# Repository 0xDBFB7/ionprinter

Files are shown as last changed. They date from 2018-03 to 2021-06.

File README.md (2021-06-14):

```
    _                       __        _  __   __  
   (_)____   ____   ____   / /____   (_)/ /_ / /_ 
  / // __ \ / __ \ / __ \ / // __ \ / // __// __ \
 / // /_/ // / / // /_/ // // /_/ // // /_ / / / /
/_/ \____//_/ /_/ \____//_/ \____//_/ \__//_/ /_/ 
```                                        

# Ionolith

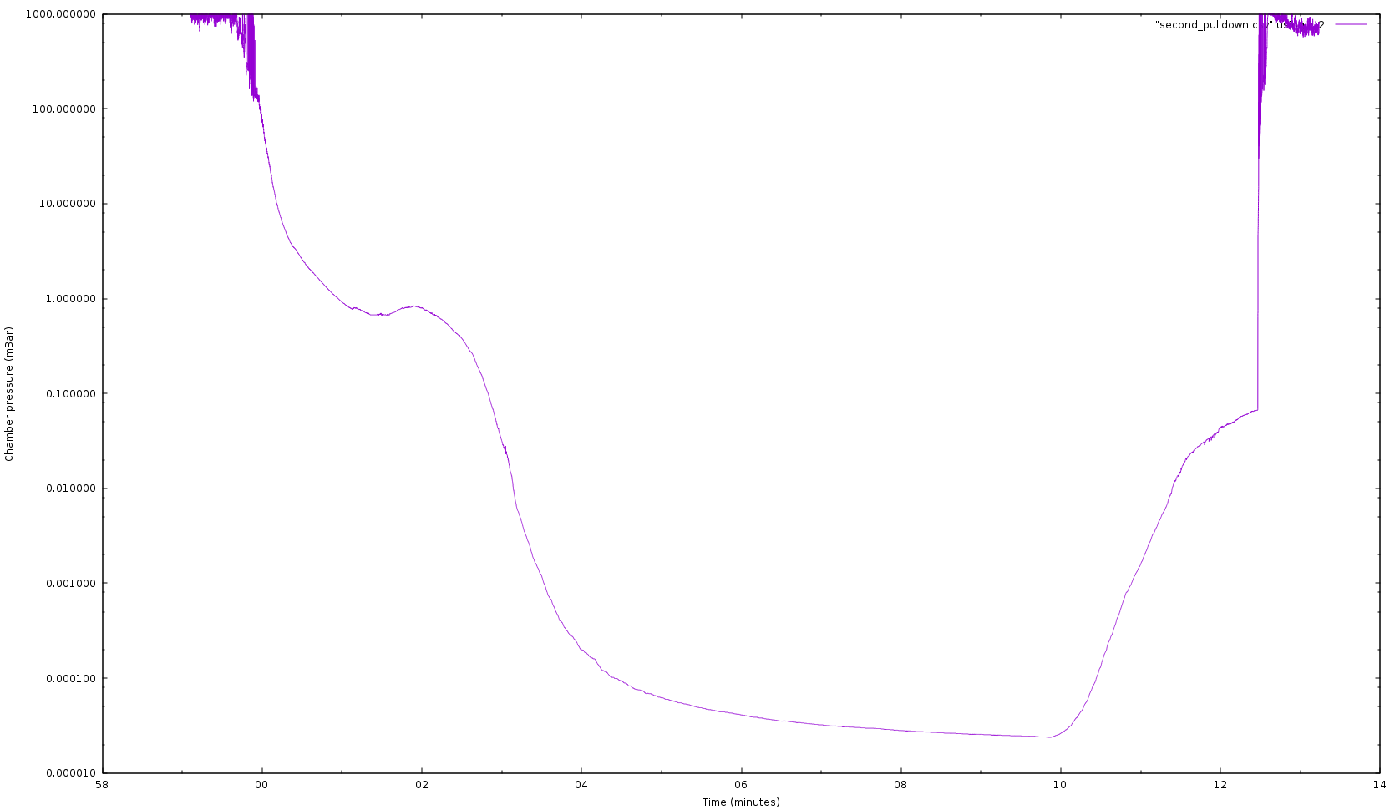
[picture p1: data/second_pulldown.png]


Hardware, firmware, software, and documentation for ion printers.

This was an extremely speculative (and arguably pseudoscientific) project to attempt to scale up physical vapor deposition beyond all reasonable limits. I got as far as building a high vacuum chamber, testing a few "bowtie" crucible designs, etc.

Spinoffs:

- a GPU-accelerated Particle-In-Cell program called [Nyion](https://github.com/0xDBFB7/Nyion) 
- A cheap silicon carbide [furnace](https://0xdbfb7.com/furnace.html)
- A cheap controller for Varian Turbo-V200 series of pumps [varian-turbo-controller](https://github.com/0xDBFB7/varian-turbo-controller)
- Control software for an Inficon BPG-400 vacuum gauge [gauge.py](https://gist.github.com/0xDBFB7/7bd7048c6639270e6f291a2673903184)

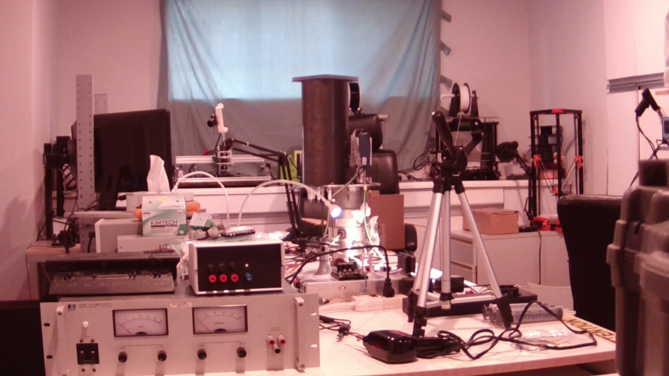
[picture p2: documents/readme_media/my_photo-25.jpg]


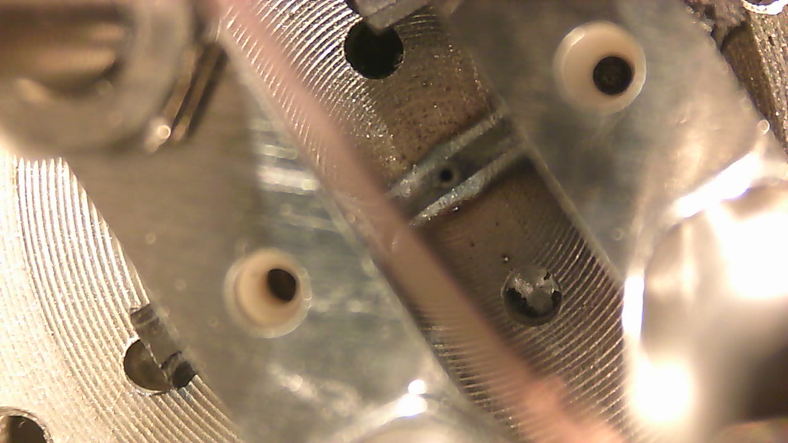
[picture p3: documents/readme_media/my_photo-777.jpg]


This whole project was far beyond my capabilities, suffers from a lack of basic physical modelling in the beam region, and so there is little basis to expect this to work.

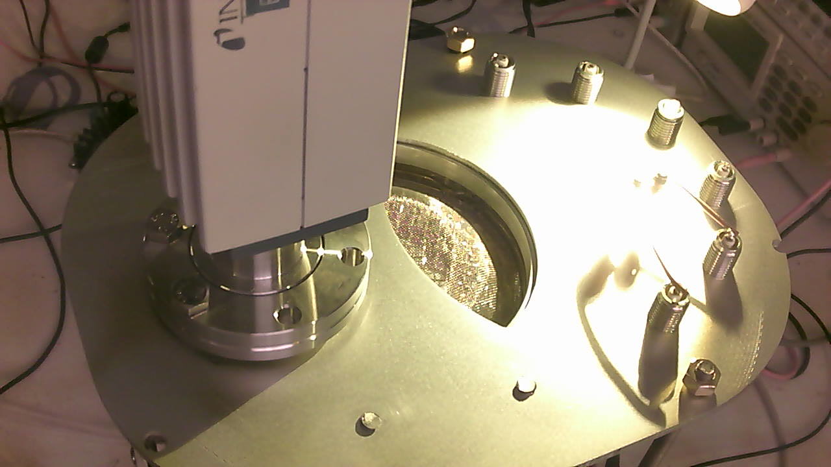
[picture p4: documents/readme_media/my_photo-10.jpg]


At the time the project was suspended, it looked something like this:

The ultimate goal was to produce an ultra high current (somewhere around 100 A of ionized aluminum accelerated to 100 to 1000 eV) heavy ion beam deposition system, aiming to 3D print large parts at cubic centimeters per hour and with arbitrary combinations of alloys and crystalline structure. 

  - Heavy ions like Al move slowly, meaning space charge effects are huge and, due to so-called "beam rigidity", magnetic focusing is useless.
  - However, this was developed under the (as yet untested assumption) that it would be possible to use a sort of active space-charge neutralization, actively injecting and confining electrons into metal-ion "packets" in the beam, to neutralize the beam space charge (something like [Gotoh 2012]).
  - Spreading the beam current over 512 or 1024 individually-controlled emitters in a 0.25 m^2 area seemed like it might alleviate deposition surface roughness issues, because of the wide range of angles of incidence.(See [Yang and Zhou, 1999, 2001])
  - Feedstock would be vaporized in "bowtie" structure - perhaps graphite-loaded magnesium oxide, perhaps coated in aluminum nitride, and with layers of ceramic multi-layer insulation to mitigate heat loss. Basic testing on a graphite bowtie was done.
  - Design goal of <$2000 cost, ideally run from a single 1500w outlet, with integrated diffusion pump.
  - Acceleration voltages over ~5000 V would pose huge X-ray and general power consumption (dozens of kilowatts in the beam!) and deposition power density (build platform overheating) issues.

```
Gotoh Y, Tsuji H, Taguchi S, Ikeda K, Kitagawa T, Ishikawa J, et al. Neutralization of space charge on high-current low-energy ion beam by low-energy electrons supplied from silicon based field emitter arrays. AIP Conference Proceedings, vol. 1496, 2012, p. 368–71.
Zhou XW, Wadley HNG. Hyperthermal vapor deposition of copper: reflection and resputtering effects. Surface Science 1999;431:58–73. https://doi.org/10.1016/S0039-6028(99)00336-2.
Yang YG, Zhou XW, Johnson RA, Wadley HNG. Monte Carlo simulation of hyperthermal physical vapor deposition. Acta Materialia 2001;49:3321–32. https://doi.org/10.1016/S1359-6454(01)00139-2.
```

For all references involved, see the file references.bib.

# <3     

# :D

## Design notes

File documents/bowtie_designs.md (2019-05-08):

```BowtieML
x = 4-40 threaded rod
(o) = alumina ionization column
o = RF coil
I = z pinch magnet
= or - or _ or O = graphite
! = copper electrode

|x|=========( )=========|x| - top graphite heater to keep ionization column warm \
    II    o (o) o    II |x|				also acts as acceleration anode?
    II    o (o) o    II |x|
    II    o (o) o    II |x|
    II    o (o) o    II |x|
      x   o (o) o   x   |x|
    ||x|| o (o) o ||x|| |x|	- nested insulators and nuts
  !!!|x|! o (o) o !|x|! |x| - copper bowtie connectors
     |x|===-_O_-===|x| 	|x|	- bowtie and injector and threaded insulators
    ||x||		  ||x|| |x|	- nested ceramic insulators 
    -----------------------	- aluminium base with blind 4-40 tapped holes
    
    Injector could be placed on the top. The top and bottom graphite heaters can be perpendicular.
    
Advantages:

Problems:
Collision with alumina wall is likely to cause high losses at high pressures.
No charge discrimination.

```

```BowtieML
Hybrid Pierce-type extractor/ICP

= - graphite
\/ - conductive but sufficiently RF transparent material - graphite?
|- - alumina insulator

			   - unspecified recombination wizardry
=====    =====
o|/        \|o - multi-segment deflection/astigmatism plates (optional)
o||		   ||o - alumina insulator ring - probably required at HV
o|\        /|o
o| \      / |o
o|  \	 /  |o - 50+kv electrostatic cone
-----    ----- - 
			   - standard graphite injection nozzle
			   
Electrostatic cone profile can be precisely adjusted to cancel out beam dispersion à la microwave dishes.

The beam must be recombined before exiting the focus chamber. 

Z-pinch and helical B-fields can be added to increase ionization efficiency; these won't affect the ions but will direct electrons. Care must be taken to ensure that these fields don't interfere with recombination.

Cone must be carefully positioned to prevent axial acceleration and the resultant X-rays. 

A phosphor+pmt interlock could be added for safety.

Why would the particles be compelled to move in a specific direction? With AC B input, would the entire arrangement not be perfectly symmetrical? 
```

```BowtieML
Hybrid Goertzel-type extractor

= - graphite
\/ - conductive but sufficiently RF transparent material - graphite?
|- - alumina insulator

			   - unspecified recombination wizardry
=====    =====
o|/        \|o - multi-segment deflection/astigmatism plates (optional)
o||		   ||o - alumina insulator ring - probably required at HV
o|-        -|o
o|--      --|o
o|- 	   -|o - 50+kv electrostatic focus structure
-----    ----- - 
			   - standard graphite injection nozzle

A reference structure is on p148 of Goerzel
```
```

```

```
      ||
      ||
      \
        \  |  |
      \   \|  |
      ||\	  |
      ||  \---|

The region where wire is injected must be colder than the melting point of the wire, else gas will escape. A large radiator can be attached to the nozzle.

```

``` 
()  = BaO coating or hot cathode
_   = high-resistance gradient deflector
--  = ceramic insulator
O   = ICP coil
[] 	= iron and mu-metal/pyrolytic graphite core and shield to prevent icp-recomb. interference
| | = graphite bowtie nozzle

   ||(     )||
   ||(_   _)|| 	    - recombination another fixed distance away
O] ----- ----- [O   - very small ~250um gap to stay within Langmuir limits
O] ----- ----- [O   - precise C-L-defined gap for ionization, +100v or so
	   | |		    - bowtie nozzle extension
 ======_O_======
 
 Entire structure can be heated to prevent deposition
```

```
:  = graphite "drawing die" injector
#  = injected wire
- 
--------------------||
-----------\		||
########## :========||
-----------/
----------------------------
 ^   	   ^	    ^ - transition to ideal vapor temperature occurs here
 |         | - transition to melting temperature occurs around here.
 |				gas-tight seal must be formed.
 | -This side radiatively cooled by graphite fins to below melting point

This may allow us to accept different gauges of wire.
```

<hr>

There are some difficulties in using ICP for this application - namely,

- Ambiguity in output particle energy spectrum
- Time-varying components leading to excessively complex simulations. Full analysis requires both small-scale timesteps to model collisions, and large-scale timesteps to model "butterfly" ion trajectories.
- Uncontrolled magnetic field - shielding from recombination current will likely be required

The main reason why I considered it in the first place was to obviate the need for a heavy and dangerous high-power, high-voltage transformer. 

However, the precise ionization cross section at 

However, the electron impact cross section for most of the elements we would choose peaks at below 

Lotz, Wolfgang. "Electron-impact ionization cross-sections for atoms up to Z= 108." *Zeitschrift für Physik A Hadrons and nuclei* 232.2 (1970): 101-107, https://link.springer.com/content/pdf/10.1007/BF01393132.pdf

```

, simple transverse-electron impact might be a simpler route.

```

```
The ion and recombination beams must be precisely matched for recombination to occur - see relativistic argument. 

The e-beam can be bent into alignment by a small magnetic field:

| / - wasted recomb. electrons
|(  - recombination point
| \ - e-beam gun

This would allow precise control over the recombination position - essential for accurate deposition.

This also allows the recombination beam energy to be varied independently, as the B-field will not affect the heavy beam.

\ | /
 )|(
/ | \

An axial field may also aid in recombination.
```

```
Low-energy design 1

After many months were spent attempting to design a focusing lens capable of 

Each bowtie is ~1mm in radius and carries 0.04 milliamps of beam current. Somewhere around 250,000 bowties will be required.

|   |   |   |   - focus and 
--o---o---o--

The bowties are arranged in concentric rings. Each ring has a different focus voltage applied passively through a resistor divider, a'la PMT electrodes.

```

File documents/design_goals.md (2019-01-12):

### Print materials

Aluminum and Copper were my target metals. I originally planned on testing with Zinc, due to its low boiling point. However, pure zinc wire is quite difficult to come by, so I couldn't do testing with injector feed systems. 

The design isn't validated with any other materials, though anything that can survive ionization (single elements, essentially - compounds will be quite thoroughly destroyed) and has reasonable boiling temperatures and ionization energies should work.

### Cost

It would suck to build this only to have it be reserved for institutions or companies: it must be affordable to the hobbyist, like current 3d printers. 

Including high vacuum pump but excluding the external roughing pump (~$200) must cost less than $1000 to build.

### Print speed

I figured 40 grams per hour was a reasonable starting point - 2.232×10^20 atoms of aluminium per second. For comparison, current FDM 3d printers can usually do somewhere around 10g/h. Since aluminum has around 3x the density of PLA, however, the volumetric print speed will be nearly on par.

Aluminum is much stronger than PLA, though, so thinner walls and lower density infills can be used.

### Power consumption

For reasons described later, power is a significant constraint. The unit should be compatible with a standard 15-amp breaker, so the maximum power consumption has to be less than 1800 watts - 1400 watts or so after power supply losses.

### Shipping

International shipping'll be insane if this thing weighs more than 15-20kg. Some sort of telescopic arrangement would be ideal.

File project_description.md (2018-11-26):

Project:
===
Status:
-------

#### Date started: 2016-??-??
#### Date finished: 2017-??-??
#### Date written: 2017-08-14

Background:
---

Description:
---

---

Thread milled the two holes for the 3/4 NPT feedthroughs - used an end mill to taper, a ball mill to finish and a 60 degree HSS tool in a boring bar to thread mill. I milled the thread in 6 passes, at 34% of 600 mm/m - 12k rpm. Coolant definitely required.

Leak.

Did a huge amount of reading (mainly Goebels et al and nasa ion thruster datasheets) over florida vacation, and I believe an inductively coupled plasma might be the way to go now. Currently, I don't really know what the charge on each droplet of aluminum is - how many atoms the vapour is composed of, etc. With a powerful enough ICP coil, I'll get full ionization for every single atom, making the math for deflection easier. With a mass flow rate of about 0.01g/s (easily achivable with the current 300w filament system), the complete ionization energy is somewhere around 500 watts. I've found an efficiency figure of 40% from a few ICP systems, so basically I need a 1kw RF supply. I think I'm going to go with an "induction heater"-style resonant ZVS royer driver - since everything's fully shielded, I don't think I'm going to have to worry about the frequency that much; and using a resonant system means I can skip antenna matching, which was an issue for me in the past. Good for testing, anyhow.

Mass flow rate: $$2.232×10^20 atoms/s, 0.01g/s$$ - about 40 grams an hour
2.407678×10^-18 j/atom - 15 ev, roughly $$1/2((29 amu)((10000m/s)^2))$$... roughly 500 watts of beam power.

Regarding the ICP ionization, the thermal velocity of the gaseous aluminum will be around 1.7 km/s, meaning at 250khz the atoms'll move around 7 mm before being ionized - if the coil isn't long enough, the atoms'll be out of the magnetic field by the time they leave.

Found an awesome paper that describes the behavior of 500khz plasmas. It seems like LF plasmas actually have some desirable properties over the standard 13.56mhz ISM plasmas, once you get past E-mode - high uniformity, etc. LF is also much easier from a generator standpoint.

I think I'm going to transition to an "untapped" royer topology - this'll mean I only need two high current feedthroughs.

A 12mm diameter 25 mm long 5-turn air-core inductor has an inductance of roughly 0.00012755 millihenries. A resonant frequency of 500 khz will require a tank capacitance of around 0.8 microfarads. I want to err on the side of higher frequency, I think, so...

Whipped up a few LTspice simulations, found I needed inductance on the input (naturally), but it seems like I could actually just use a h-bridge on the high side...

Tested out the chamber a few more times, still leaking at the feedthroughs. Need to re-design them.

<lots of stuff happens off-camera>

Oh jeez.

This is going to have to be fast.

Really fast.

With a 100g/h deposition rate, a 10 mil dot size, and reasonable Z resolution of somewhere around 5 mil, the slew time of the deflection supplies will have to be under 50 us.

With a 10 mil dot size over a 1 cm deflection (400 steps), the slide will have to move at around $$1 cm/ 20 milliseconds$$ - around 40,000 mm/min. This seems just barely achievable with stepper slides.

With those same values and a requirement of 5 bytes per point, the software will have to stream points at nearly 100kbps. That seems achievable too. Proper curve fitting etc will also reduce that.

Values I'll probably have to update live:

- Beam X Y position, focus, astigmatism.
- Stepper X and Y position.
-

RF power, beam current, diffusion pump power, etc will presumably be set before a print.

I'm kind of coming to grips with how monumental the realtime requirements for this thing will be. I don't think I have any time to stream values to different processors - I think I'll have to abandon my original modular idea and make everything run on one STM32.

Now, the deflection amplifier.

Someone on phys.se raised a good point: at low acceleration voltages, how will stray magnetic fields affect the beam?

Since the magnetic force on a moving charge is F=qvB, the fuzzing due to magnetic fields should actually go down - but let's make sure.

At 48 eV, Aluminum will travel at 18,528 m/s. qvB at 100 gauss = -3×10^-17 newtons. The particles will take 2.7×10^-5 seconds to travel 0.5m to the build plate. This means that the beam will be slewed

0.5 * 6.695846×10^8 meters per second squared * (2.7×10^-5s)^2 = 0.2 meters.

Darn.

At 1 gauss, about 2.5 mm.

The deflection seems to be unrelated to V, but I know that this is impossible, since 30 kv CRTs aren't affected by the earth's magnetic field.

I must have something wrong in my reasoning. Going again:

(0.5*(((sqrt(2r)/sqrt(m))*b)/m)*(d/(sqrt(2r)/sqrt(m)))

Where r is energy, in eV.

R just falls out of the equation:

(0.5*b*d)/m

And so I am correct in that voltage is unrelated to magnetic deflection.

Wait, what?

Okay, looking it up, I'm totally wrong. The actual equation is:

X deflection = (0.5bd)*sqrt(q/(2(v)m))

Where v is volts. This means:

(0.5*(100 gauss* (0.5m)^2)) * sqrt(-(electron charge)/(2*48 volts *(27 amu in kg))) = 0.2 m.

At earth's magnetic field and 1000v, we get 0.1 mm. 100v: 0.5 mm. 48v: 0.7mm.

10 Gauss, 0.1m distance to build plate, and 48v: 1mm.

Now that, I believe, is fine - that's an N52 magnet at 0.1 m. Steady state components can be calibrated out, too - I'm mainly just worried about oscillating magnetic fields due to the RF coil.

With 150a going through the coil, there'll be a roughly 1.5 gauss field oscillating at 6 in away.

I can put a bunch of hall effect sensors in different places in the chamber and try to compensate for fields measured.

Aha! Existing induction heaters use inductors on the high side. When a piece of metal enters the coil, the frequency drops significantly - giving the inductor more time to allow more current through, increasing the power draw and dissipation. Cool!

Huh, wait. Why can't I just ionize the aluminum with bare +48v? The ionization energy of the aluminum is only like 15eV. If I can strike the arc with a few kilovolts (like a fluorescent tube), I should be able to ionize everything that goes through...

Hmm. Perhaps that "striking" effect relies on the gas already being ionized. That would make sense - but it'd also mean that I can't do that, since the gas is constantly being replenished.

Had an enlightening discussion on The H Bar about this striking effect; apparently it is related to the electron drift rate, and is likely to work on a stream of gas. Also, in 20170210_100824.mp4

When my milligram balance comes in, I'll try running a test with +48v and see what kind of ionization I can get - deposit onto a plate, measure the charge, weigh the plate, and divide by atomic mass of aluminum.

Going back to my graphite "bowtie" filament/crucibles; I can't find a reliable source on the resistivity of graphite, suprisingly enough; it seems to vary wildly between batches and processes. Measuring my block from McMaster, I get a value anywhere between 10 and 0.3 ohms with varying contact pressure. The block is 20.5 cm long by 2.5cm wide and 0.7cm thick. To get a slightly better reading, I connected up my Korad PSU to both ends and set it to 0.5a. This gave me a voltage of around 50-70mv and falling, for a resistance of around 1.5 ohms. Scaling that roughly to my previous bowtie's area, I get about 0.8 ohms. This explains why I didn't get good results with my previous bowtie tests at 20v; I'd only be drawing a few hundred watts. I'll have to try again with a smaller bowtie and with my new PSU.

Ooh, I could SPTM the graphite crucible! Nah, I don't need to.

Re: Speed: at 1Mbps, (about the peak for STM32 usb), transferring 1 point (6 floats; 4 bytes per float, no encoding) would take about 200 microseconds, plus response, which is longer than my target 50 us value. I guess I'll really have to fill up that buffer beforehand.

It seems like my ICP coil inductance value is incorrect: a more accurate value would be around 1 uh.
jb weld

Darnit. Another first-principles error; and I know why my many graphite/filament tests weren't working. With a surface area of 808 mm^2 (the v2 bowtie), and a temperature of 3070 K,
the bowtie will be radiating *nearly 4 kilowatts* as heat; the Stefan-Boltzmann law goes as the 4th power of temperature. The emissivity of tungsten is 0.04, which makes for a loss of 160w with the same area.

If I can get the bowtie surface area to below 20 mm^2, I'll only have to
contend with 100w of radiative losses, which seems manageable. Power budget is being eaten into a bit, but oh well.  I could also try using an aluminum reflector to increase efficiency;
aluminum is 87% reflective at infrared.

GAH; another bloody problem. If an alloy is injected into the bowtie, the different molecular masses will cause a "mass spectrometer" effect in the deflection plates, blurring the deposition horrendously.
Since we need to deposit all the materials in the alloy simultaneously, not sequentially, multiple bowties with multiple accleration voltages tuned to their respective masses would work.

Wire feedthroughs: Buna-N has a TML of around 7; I don't even have to worry about a tiny bit of JB-weld, I don't think.

The Bowtie; the graphite that I purchased from mcmaster has an exceptionally low resistivity; around 1.54×10^-5 ohm meters. This means that a 10mm long 4*4mm rod would have a resistance of 0.0385 ohms,
drawiing 20a at 12v. When the injector holes are drilled, and some extra contact resistance is added, this is almost perfect...though this bowtie would also have an area of 80mm^2; a loss of 400w.

Might have some issues dissipating 500-odd watts of beam power in a cm^3 scale part. Liquid-cooled or cryo-chilled build platform might be required.

Even at a super slow print speed of 0.4 g/h, a 1 oz PCB will be done in 17 hours.

A serious problem: the beam current density is much, much higher than standard particle accelerators. A typical value seems to be 50 A/m^2; with a beam diameter of 0.5 cm, the initial beam current density will
be nearly 125,000. A beam diameter of 1 cm will yield a current density of 31,800; but the electrostatic optics become problematic at these charge density levels.

So, I either have to decrease my beam power (how?), or figure out how to focus at that power.

I could split the beam into seperate beams, each with a lower energy...

A small dot size is only required for fine details, where the print speed can be lower.

Some simple math: 40g/h of aluminum, which is 15 cubic centimeters (a cube 2.46cm to the side).

Tested the micro stepper injector motor: good torque at raw 5v from an arduino even up to 240rpm. It has an unusual 8-10-9-11 pinout, strangely.

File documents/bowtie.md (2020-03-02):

# The ion printer first requires a thin, vaporized jet of the target material. 
## This page describes the element that creates this stream.

### Why the hell do you call it a "bowtie"?

The original prototype of this element bore a close resemblance to a bow-tie:



Bowties are cool, and I love me some whimsical industry-specific jargon (c.f. [salad-bowl](http://projects.astec.ac.uk/ERLPManual/index.php/Photo_Cathode_Heat_Cleaning), Schlooping). "Filament" is ambiguous - there are at least three other filaments in use. I'm sure there's some accepted industry-standard name for this kind of thing, so call it whatever you want.

### Wait, isn't this already a solved problem?

While thin-film PVD boats and baskets exist, they really aren't a good fit for this device for a few reasons.

* Firstly, and perhaps most importantly, they don't produce a thin stream of gas. They produce a cloud of atoms with essentially random direction. This might not seem like a huge deal, but it's what took the majority of the time developing the ion printer. You might think that a nozzle or aperture would work; but your nozzle has to also be heated to above ~3000 K, else all your gaseous aluminum sticks to the nozzle and rapidly prevents operation.
* Secondly, while even more specialized solutions may exist, they're bloody expensive. Even cheap tungsten boats seem to start at ~$100 - far too expensive for a consumer device.

### Required temperature

https://www.iap.tuwien.ac.at/www/surface/vapor_pressure

The vapor pressure of the desired print materials is low at low temperature.

Therefore, to get a bearable print speed of >50g/h, it can be assumed that boiling is required. 

### Why not use induction heating?

I spent a few thousand hours trying high-power induction heating methods (largely based on some papers I've since lost and [1]). Induction heating, however, has a few serious drawbacks compared with simple Joule heating:

* Low effectiveness on non-ferrous metals. Metals like iron love induction welding, due to their high relative permeability; Aluminum doesn't absorb current as well; sure, you can get a chunk of aluminum up to 800c or so with 10kw of power, but we don't have the luxury of such high powers.
* Low effectiveness above the Curie point. Metals generally lose a lot of their magnetic properties above a certain temperature; that temperature is far, far below their boiling point.

It may be possible to build an ion printer that uses induction heating, but there aren't many benefits.

### Why even use a filament? Why not just vaporize the material itself?

First of all, if you just apply a few kilowatts to some aluminum, it will simply melt apart, breaking the connection. This might seem simple to mitigate, but I couldn't find a way to do it. A sharp rising edge in the power domain is therefore required.

I did quite a bit of testing with large capacitors in an attempt to accomplish this, which was mildly successful. You can pretty easily dump a few KJ into some aluminum wire to get gaseous aluminum. Unfortunately, there's one serious issue with this: it's non-directional. Everything in the line-of-sight gets coated in aluminum, which is undesirable for long-term usage; it also becomes extremely difficult to form a beam with a spherical vapor cloud. It *may* be possible to electrostatically pull a cloud of neutral aluminum into a coherent beam, perhaps with an ICP coil surrounding the whole lot, but I gave up on this method.

### Some simple physics background:

To reach the boiling points of metals, extraordinarily high temperatures are required, and so heat loss minimization is paramount. Some ways that the bowtie will lose heat:

#### Convection

The bowtie is in a high vacuum, so thermal convection can be entirely neglected.

#### Radiation

Anything hotter than absolute zero radiates away thermal energy in the form of infrared radiation; the amount of energy loss is given by the [Stefan-Boltzmann Law](http://hyperphysics.phy-astr.gsu.edu/hbase/thermo/stefan.html).

This is proportional to emissivity and heated surface area, and goes as the 4th power of the temperature.



This power loss is quite significant. 

#### Enthalpy

Aluminium:

| Source | Energy requirement |
| --- | --- |
| Heating | 0.9 kJ/kg/K * 2500 degrees = 2250 kJ/kg |
| Fusion | 398 kJ/kg |
| Vaporization | 10.5 MJ / kg |
| Total | 13.15 MJ/kg |
| @40g/h | 144.7 W |

A print speed of 40g/h will require at least 144.7 watts to be input to the bowtie. Values for copper are similar.

### Tungsten filaments

#### Tungsten has a few things going for it:

* Insanely high melting point (3800K or so); essentially anything you could possibly want to vaporize could be done with a tungsten bowtie.
* Low emissivity (0.05 or so); this means that very little of your energy 
* It's already commonly used for thin-film thermal PVD systems
* It's inexpensive and readily available in the form of "Green" TIG electrodes.
* It's relatively inert, and won't react substantially with filament material

#### It's also got some pretty serious issues:

It's very difficult to work with. It's one of the hardest materials around, which makes conventional subtractive manufacturing processes nearly impossible; EDM/[ECM](https://nptel.ac.in/courses/112107077/module3/lecture15/lecture15.pdf) seems to be required. Standard casting techniques don't work; a complex high-pressure sintering process is required. There are many companies around that will wrangle this metal of Cthulhu to your desires, but that takes us far from the protective margins of vertical integration.

You might wonder why we even need to work the tungsten at all. Indeed, just winding some aluminum wire around a 1/16" tungsten rod produces a small bead of molten aluminum, which then evaporates. Unfortunately, this has the same problem as the capacitor discharge system above; it's not a directed stream of gas.

However, there is one process you can easily perform on tungsten: you can bend it. Though its melting point proper is high, it becomes very ductile at comparatively low temperatures; ~1500c - easily attainable with an acetylene torch. 

In retrospect, this seems obvious, but I learned it relatively late in the project.

A layer of yellow tungsten oxide forms when bending, which can be eliminated by using an inert (nitrogen, in my case) or endothermic atmosphere, but this layer quickly evaporates when the finished product is heated in a vacuum.

My final tungsten design was a cylinder wound using 1/16" tungsten rod, with a graphite plug at the bottom. This worked reasonably well. However, the efficiency and rate of vaporization was quite poor; with my high-current transformer, I was only just able to get to the boiling point of aluminum.

### Graphite

Graphite, on the other hand, is easily workable with standard machine tools. However, this comes at a cost:

* Poorly-defined properties. Graphite's electrical and thermal conductivity is dependent on a large number of factors, including grain size, production method, contact pressure, impurities, etc. It's even anisotropic; measuring resistance lengthwise or widthwise can return a different result. 
* More reactive. Graphite is prone to reacting with metals at high temperatures, though it remains to be seen how much of an issue this will be. The bowtie is likely to be an inexpensive consumable for this reason. 

Graphite also sublimates at high temperatures; its vapor pressure is between 10 and 100 Pa at the boiling point of aluminum.

There's kind of an issue here. Making the supports thicker decreases their resistance, allowing the crucial center section to become hotter; but it also increases their thermal conductivity proportionally, wicking heat away from the center section.

#### Ceramics

Thermal conductivity.

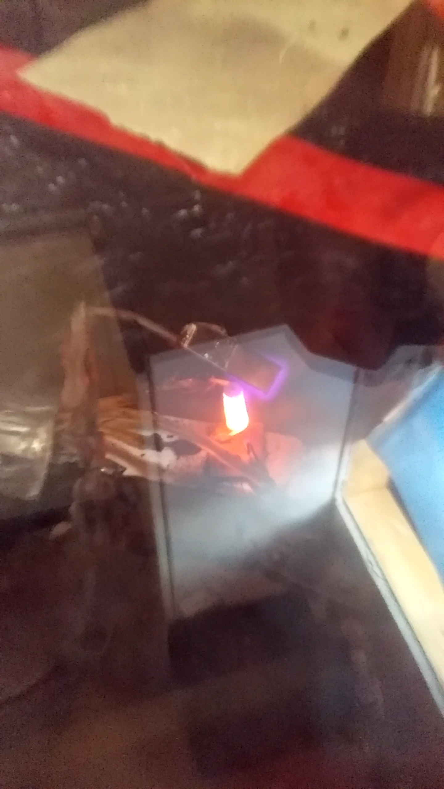
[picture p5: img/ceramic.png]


#### Zinc crucibles

For initial exploratory research, I attempted to vaporize zinc in my Gen1 and Gen2 test chambers, due to its ease of boiling. This worked okay, and helped me understand more about how how the vapor paths would work.

I attempted a number of zinc crucible designs, including using off-the-shelf heaters, sand resistors, etc, and finally settled on this one:

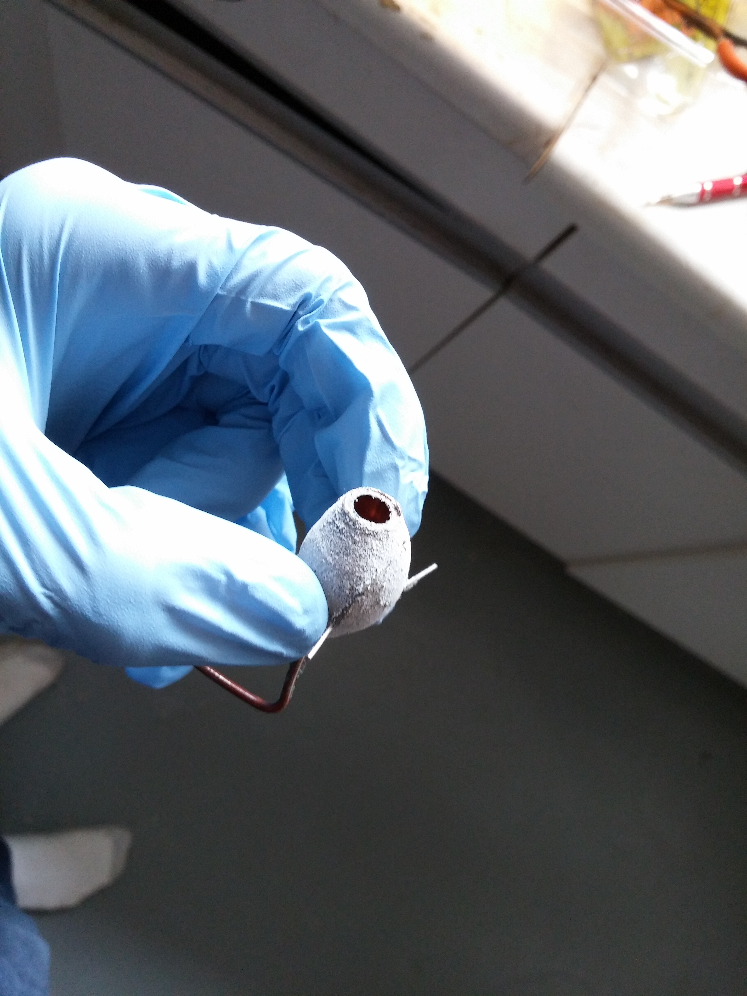
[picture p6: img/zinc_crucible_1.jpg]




It's a pretty simple construction: a copper tube, crushed at one end, then covered with a thin layer of high-temperature fire-cement to form an electrically insulating layer. After a few minutes in an oven at ~75c, a dozen or so turns of Kanthal A1 resistance wire were wound around this insulated slug. This, then, was also covered in fire-cement, then baked over the course of an hour at slowly increasing temperatures to prevent cracking. Once in a vacuum, I thermally soaked it at ~600c by applying current to the Kanthal. I then added a few grams of zinc and applied as much current as I could to begin zinc vaporization. A high voltage was applied to the copper tube, allowing the vapor to retain a partial charge.

This has a number of issues.

* The soak procedure is very time consuming, but is required to prevent immediate cracking.
* The crucible would still be spent after every single test due to cracking and porosity.
* It cannot possibly be used for copper or aluminum.

Thermal conductivity

### Temperature control

The rate at which the material is deposited is equal to the power put into the bowtie divided by the enthalpy of vaporization of the metal, minus losses and thermal mass. 

It would be nice to be able to determine the temperature of the bowtie. 

#### Thermocouples

Standard K thermocouple wire can't be used, as it'll melt. Some esoteric W/Rh junctions can handle the heat.

#### Bowtie resistance measurement

The resistance of most materials changes in a well-defined manner as the temperature increases. Ohm's law can be used to calculate this resistance based on the current draw at a certain voltage.

#### Bolometers

As far as I can tell, no off-the-shelf infrared sensor is capable of measuring these insane temperatures.

#### Emission spectroscopy/pyrometry/radiometry

The black-body radiation spectrum is shifted as the temperature increases. By measuring the spectrum at multiple points (two phototransistors with IR-cut and visible-cut filters, say), an accurate reading of the spectrum can probably be made. 

### Simulation

Oh! I can simulate this by using a heat flux boundary condition!

### Exit gas parameters

The gas that exits the bowtie has a certain temperature distribution. 

[1]: http://www.rmcybernetics.com/projects/DIY_Devices/diy-induction-heater.htm

The primary reason for the large array of small emitter bowties is to reduce the space-charge forces before neutralization. 

The pressure required in each bowtie is also far lower. This eases simulation, as the high Knudsen number avoids turbulent effects and allows simple rarefied-gas monte-carlo methods to be used.

Ostensibly it also reduces the current density requirements for hot cathodes, but this isn't really a design driver.

High pressures would also mandate temperatures well above the boiling point of the print material, which would complicate things from a materials science viewpoint (by accelerating interfacial reactions, increasing vapor pressures), produce messy, ill-defined vapor that could be contaminated with macro-scale droplets (as learned from early zinc testing), increase power consumption (though this may be offset by the greater surface area), and require that all upstream systems be gas-tight, rather than simply optically opaque. 

/ It also simplifies the collimation of the vaporized material; a simple multi-stage gas lens is sufficient for this regime. 

Because the bowties approach the part from different angles, this also eliminates the need for a linear stage to move different faces of the part into line-of-sight. As long as the print array is slightly larger than the part, 

The arraying also happens to be very helpful for surface physics. First, the surface power flux density (W/m^2) is more variable, allowing the deposition temperature to be precisely controlled. This is essential for control over the crystalline structure of the print. 

The wide range of angles is also essential to prevent defects from propogating. A single beam will tend to exponentially amplify any pits and lands in the substrate, whereas the array will provide a smoothing set of lines-of-sight.

It also allows us to accomodate a wide range of materials simultaneously.

All this comes at the cost of complexity in feedthroughs, larger vacuum chamber volume, higher surface area to clean, control and feedback bandwidths, and common-beam repulsion effects.

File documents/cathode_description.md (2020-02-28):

# Hot Cathode

-check it and see

*ahem.*

### Introduction

Hot cathodes produce a cloud of electrons via thermionic emission. We need a bunch of electrons for a number of processes: 

* For discharge ionization, to catalyze sparking an arc across the ionization chamber via townsend avalanche
* For plasma recombination, to neutralize the exiting ions.
* For vacuum tubes?

There's two main types of hot cathodes: directly and indirectly heated.

The effectiveness of a hot cathode depends on the temperature and the work function of the surface material. The work function of raw tungsten is around 
$$
4.5eV
$$

 much too high for our purpose. 

Oh, and it doesn't seem like you can buy either coated wire or paste off the shelf, so we'll have to do this ourselves.

### The ionizer cathode

To my current (ha!) understanding, electric arcs form when a few initial electrons (typically ejected from the electrodes via cold cathode effects) collide with the intervening gas particles with enough energy to liberate an electron from each. A chain reaction then occurs, where each electron ejected from an atom collides with (on average) one other atom. 

There's a whole bunch of nuance to be added here regarding electron drift velocities etc. I'll get to this part in a bit.

I don't yet know how many electrons we'll need for this section.

<hr>
### The ion curtain cathode

Hope that joke isn't

over the line

Our target print speed is 2.232×10^20 atoms/s.

To make our lives easier, I think we'll want at least double the electrons at the ion curtain in order to guarantee complete neutralization of the beam; so let's aim for 5×10^20 electrons.

An amp is a Coulomb per second, and 1 Coulomb is equal to around 6.242×10^18 electrons. Therefore we will require somewhere around 80 amps of emission current.

Using equation 14 in [2],

$$(1.2x10^6 A/(m^2 (kelvin^2))) * (((1000 Kelvin)^2)*exp(-((1eV)/(Boltzmann constant * (1000 Kelvin)))))$$

This yields a current density of around 

Hmm, that's not quite right.

Page 10 of [1] provides the following value:

> If modern highpower
> valves are considered, especially those designed for shortwave
> operation, it is found that they are operated with current
> densities between 100 and 300 mA/cm^2 (average D.C.). A very
> high momentary current density is drawn from cathodes for pulsed
> operation, especially from those in magnetrons. The peak values
> obtained in this case are between 10 and 30 amps/cm^2

Source 4, from Wikipedia, states the following value:

> Oxide filaments - 10 A/cm2

Assuming a typical value of 5A/cm^2, we will require a 16 cm^2 cathode; about 6 meters of 0.08mm OD wire - if coiled with a 2.5mm radius, 400 turns. Perhaps an indirectly heated cathode would be a better choice.

Separately, from [4] we find

> 500 mA/W

And so heating this behemoth of a cathode will eat up ~160 watts of our power budget, plus whatever power is required to accelerate the electrons into a proper curtain.

By measuring the ionization current with the cathode hot, we conveniently get a marginally effective high vacuum gauge for free. As you might imagine, the hot cathodes described here cannot be run in low vacuum, so we'll have to figure out some other method of measuring vacuum in the micron range. It might be possible to use the bowtie itself as a crude thermocouple gauge, measuring convective heat loss.

There's a whole bunch of factors that go into making a reliable, long-life cathode, but we have the luxury of being able to replace the cathode in short order, since we have a vacuum pump and a resealable chamber. Worst case scenario, if I am unable to improve the lifespan, the cathodes can be a cheap consumable. Even a 200 hour lifespan would be more than sufficient. This also lets us drive the cathodes a lot harder and get a higher specific power.

The vapor pressure of barium is quite significant at these temperatures. Certainly something to look out for.

[1]:

> "When discussing the manufacture of the emission paste the
> necessity of using pure materials and clean processes cannot be
> emphasized too strongly. As shown later, very small additions of
> foreign materials to the emission paste may influence the emission
> decisively, giving rise to a deterioration of emission in nearly all
> cases (cf. Vol. II, Sec. 26.2)."

Hmm. Seems like I might encounter some difficulty with this process.

[7]:

> The early tubes were all equipped with tungsten filaments. The filaments were low cost
> and performed very well. However, on many occasions, the operators forgot to turn the ion
> gauge tube OFF before letting the system up to atmospheric pressure. When the oxygen in the
> air reached the hot tungsten filament, it cause instant oxidation and burn-out of the filament. The
> tungsten oxide which forms on burn-out covers about half of the inside of the glass bulb with a
> creamy white coating which is easy to recognize. The solution was to find a filament material
> which did not easily oxidize, even when exposed to atmospheric pressure when hot.

This won't really be an issue for us, since our repressurisation will be automatically sequenced.

Contrary to standard vacuum tubes, we don't actually care about cathode lifespan very much; cathodes can be a cheap consumable.

[^10]

> The cathodes can be made to give usable
> emission in demountable systems by increasing their temperature (thus shortening the life very considerably)

***

Okay, so let's look at all our cathode options. [10] provides a good summary.

| Material | Work Function | Typ. Emission | Efficiency | Operating temp. | Resistant to poisoning | Vacuum level required |
| --- | --- | --- | --- | --- | --- | --- |
| Pure tungsten | 4.54 eV | 4A/cm^2 | 17.5 W/A (1400w) | 2400K | :heavy_check_mark: | |

Tungsten wire is cheap and readily available, but the low efficiency is killer.

| Material | Work Function | Typ. Emission | Efficiency | Operating temp. | Resistant to poisoning |
| --- | --- | --- | --- | --- | --- |
| Thoriated tungsten | 2.7 eV | 4A/cm^2 | 6.25 W/A (500w) | 2000K | :heavy_check_mark: |

Again, readily available, and again a really abysmal efficiency. Good enough for testing, perhaps.

| Material | Work Function | Typ. Emission | Efficiency | Operating temp. | Resistant to poisoning |
| --- | --- | --- | --- | --- | --- |
| Barium Oxide | 1.5 eV | 0.5A/cm^2 | 2 W/A (160w) | 1100K | |

Oxide cathodes are apparently a little tricky to make.

.[^5]: 

> One drawback of oxide-coated nickel is that it is one use only. Once the system is let up to air, the cathode must be replaced. This is a problem in demountable systems where test elements within the system must be changed occasionally.

.[^1]

Contrary to the above, however, oxide cathodes are, in fact, demountable, if operated at a higher temperature and maintained at 120c when exposed to atmosphere in order to prevent water absorption.

Barium oxide is *quite* toxic. Might not be ideal for consumer use.

Barium aluminate is pretty safe.

***

 * [^1]: Herrmann, Günther, and Siegfr Wagener. The oxide-coated cathode. Vol. 2. London: Chapman & Hall, 1951.1.
 * [^2]: Grilj, Marjan. "Thermionic emission."

[^3]: [internal](../references/filament_coatings.pdf)
 * [^4]: L.W. Turner,(ed), Electronics Engineer's Reference Book, 4th ed. Newnes-Butterworth, London 1976 ISBN 0408001682 pg. 7-36
 * [5]: http://ebeaminc.com/thermionic-cathodes.htm
 * [6]: https://ntrs.nasa.gov/archive/nasa/casi.ntrs.nasa.gov/19760024327.pdf
 * [7]: https://www.duniway.com/images/_pg/hot-filament-ion-gauge-tube.pdf
    https://electrontubestore.com/thoriated-tungsten.pdf
 * [^8]: Criado, E., et al. "Ion beam neutralization and properties of plasmas from low power ring cusp ion thrusters." Physics of Plasmas 19.2 (2012): 023505.
 * [9]: http://www.imajeenyus.com/vacuum/20060813_thermionic_emission/index.shtml
 * [^10]: Jenkins, R. O. "A review of thermionic cathodes." Vacuum 19.8 (1969): 353-359. [Internal](../../references/jenkins1969.pdf)

[^5]: ebeam Inc. - Thermionic Cathodes [Internal]() [External](http://ebeaminc.com/thermionic-cathodes.htm)

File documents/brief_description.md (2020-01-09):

### Project Ionolith

##### Brief description

Wait, why not publish it? If the technique is unfounded, then I will waste a great deal of scientists time, and  

> Reality must take precedence over public relations, for nature cannot be fooled. - *Feynman*

Behold, the central thesis of the *Ionolith*:

Less facetiously, this technique is known as ion beam deposition (or lithography). It is currently limited to producing objects at a scale of angstroms per hour, and the machines cost many millions. 

Very unfortunately for my studies, parents, and mental health, I've been unable to conclusively demonstrate that it is entirely impossible to simply scale this up to $\text{cm}^3$/hour with a $1000 consumer machine, despite 3 years and 1,600 papers.

This is almost certainly impossible, of course, since nobody is doing it; but it's such an absurd and fantastic problem that I've been unable to stop working on it.

I am buoyed by the fact that a very closely related thin-film technique called Physical Vapor Deposition was once demonstrated to produce millimeter-scale layers.

Even when it ends up being impossible, I have learned a great deal from the process; so I'm not altogether concerned about when that day comes - though I must admit to hoping that it won't.

### Problems in order of difficulty

#### Space-charge neutralization

Feynman mentioned ion beam lithography offhand in his 1969 lecture *Plenty of Room at the Bottom*, remarking that it was probably impossible to scale up to anything macro because of space-charge effects.

To see why, let's compare with a CRT screen again.

The ions we're trying to print are about $10^5$ times heavier than electrons, and so they move commensurately slower. Current theory predicts 250x slower.

The electric field created by the space charge is proportional to the velocity; so the gradient is that much higher. 

Compounded with these difficulties are the limited power consumption and target heating, both of which demand a low per-particle energy of ~100 eV.

Physics does not demand space charge, however. There are many 

Largely due to progress in accelerator science, the prevalence (ha!) of industrial ion-beam implantation systems for semiconductor doping, and  a great deal has been learned about implementing space charge neutralization, compensation, and beam cooling since Feynman's talk.

The simulation detail required to resolve these effects did not exist at the time. 

The current design somewhat mitigates this issue with a massively-parallel many-beamlet design; but this may be completely wishful thinking.

*It is entirely possible that this is unreasonable.* There are many regions of the beamline that are still opaque to the horribly crude zeroth-order analysis I've been able to produce so far.

#### High-performance multiscale multiphysics simulation on consumer hardware

##### Status: almost certainly solved. Demo implementation in-progress, but with very recent developments in half-precision computing and improvements in memory bandwidth.

'common-beam' effects. 

DSMC

#### An inexpensive, 'demountable', user-friendly high vacuum system

##### Status: not an issue.

This turned out to be the easiest part of the whole system; in fact, I have a system built from scrap for \$250 that easily attains $10^{-5}$ mBar. 

Together with ceramic techniques from below, 

Attempts to build diffusion pumps have revealed a ludicrously simple construction belied by their high prices.

Because of the temperatures involved, the contamination that  the bane of all are not expected to cause difficulty.

#### Dirt-cheap high-temperature ceramics with arbitrary geometries capable of continuously withstanding superheated metal.

##### Status: Partially solved. A process for sintering gelcast aluminum oxide / graphite composite parts has been demonstrated with very acceptable economics. Candidate linings (aluminum nitride), have been found; 

The typical gaseous vapor source for PVD is a tungsten boat. These are far too expensive for a consumer product; tungsten is neurotoxic (necessitating expensive industrial hygiene) and stupendously difficult to work with. 

Moreover, W's low resistance coupled with the required geometries mandates heavy, copper-filled transformers and high-current vacuum feedthroughs. 

To add even more difficulty, current tungsten boats are only designed to produce the faintest wisps of vapor. The vapor pressures required to produce macro-scale objects require much higher. 

Simple tests with micro-machined graphite piping 

Even more concerning is the fact that superheated metals dissolve almost everything; only precious few materials can withstand prolonged exposure. Aluminum nitride is particularly convenient. 

Still more concerning is the tremendous power consumption. The enthalpy of vaporization of the metals is only contributes a small fraction of the. 

#### Surface effects: crystalline structure, ad-atom reflection, sputter yields, skitter

It remains to be seen if so-called depressed collector systems will work.

#### Inexpensive, high frequency, high voltage precision electronics for beam control

The current design calls for 1024 to 2048 individually-controlled beamlet emitters, with approximately 8 electrodes that must switch 5Kv at a few Mhz within a tolerance of a few millivolts.

That number of high-voltage MOSFETs would already break the budget.  

Feedback looks to be achievable via beam modulation, coupling into electrostatic beam position monitoring buttons.

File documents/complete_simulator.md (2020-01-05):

It is important to note that the author is not an expert, nor a trained physicist. Much of this document is written from memory, and should certainly not be used as an authoritative source.

The goal

Accurately simulate the electron and heavy ion motion in the beam, to rapidly test designs.

Simulate diffusion pump nozzle.

Optionally, compute stresses, 

The great part is that once this simulation is complete, it can be used to validate the control system, and ensure that prints will complete safely.

To do this, the following physics must be simulated:

- Ionization
- Electric field
- Vaporization (print material, contaminants, graphite from bowtie structure, and diffusion pump oil)
- Joule heating and heat transfer
- Particle deposition, condensation, and crystalline structure formation
- Forces and collisions between ions and ions, ions and electrons, electrons and ions, and the trace background gas in the chamber.
- Optionally, a magnetohydrodynamic system.

The whole system must also be usable on common hardware; in the spirit of open-source, owning only an Ionolith and a reasonably-powerful gaming computer must be sufficient to simulate the beam, since the end-user may wish to make improvements, use untested materials and alloys, etc.

As we'll see later, this eliminates many options outright. CUDA-only frameworks like AmgX, and PICOnGPU.

There are many ways to simulate a beam of charged particles. In order of computational complexity,

Unfortunately, closed-form equations don't exist for electric fields; you can't just plug numbers into a formula and get a particle trajectory. 

The problem is equivalent to the fringe-fields you may have learned about in high-school physics, where the simple capacitor equations break down.

#### Transfer function codes

##### Examples: TRACE-3D, TRANSPORT

Certain simple beam devices (such as Einzel lenses Gillespie, 1997, Rashid, 2011) can be represented by an equally simple analytical function that alters the velocity and position of particles accordingly. 

These are analogous to geometric optics, where light is assumed to travel in straight lines. Unfortunately, these models fail miserably with the complex, low-energy beams used in the ionolith, and also restrict the geometry of electrodes to a limited number of shapes.

#### Envelope or 'slicing' codes

Assuming a homogeneous, cylindrical beam, 

#### Vlasov codes

##### Examples: IBSimu

These generally converge the entire beam trajectory at once, forming a probabilistic model of the beam. It is difficult to integrate collisions with 

[note: research Vlasov more]

#### Particle-In-Cell codes

##### Examples: Warp, WarpX, PIConGPU, QuickPIC, AlaDyn, SMiLEi, Piccante

##### Examples: Pic-Las, V-sim

### Discretization

Many codes (such as SIMION) support many of the simulation modes described above.

Sympletic methods RK4 periodic correction

### Finite-difference-time-domain

##### Examples: gprMax

In conventional 3d electrostatics, we discretize in 3 dimensions, solve, apply changes to electrodes and move particles etc, then solve again, ad infinitum. This works for most time-invariant fields; electrostatic fields, magnetic fields, etc.

Magnetic fields can be found by solving for the current in conductors in each direction (x,y,z), then solving three seperate poisson equations for the same.

It's even possible to simulate time-varying electrostatic systems (like capacitor impedance) in steady-state by supplying assumptions about frequency and amplitude in the boundaries. See [] for more on that.

Likewise, it's possible to simulate the time behavior of heat transfer, 

However, coupled *electromagnetic* fields involve time-varying quantities proper; it's impossible to calculate 'a single step' of the field. For instance, see Maxwell's equations, like
$$
V = -\frac{dB}{dt}
$$
You can't usefully apply this to a mesh without time.

Designing inductively-coupled plasma coils requires the above equation. The time-varying magnetic field induces an axial electric field in the vacuum, which accelerates electrons to bombard neutral gas. This is the main reason why a second electron gun is used for ionization in the first-gen designs; it's ostensibly steady-state. 

This actually constrains our hardware design solution somewhat. If we can't usefully simulate an ICP coil, for instance, we can't deduce the nuances of how the particles will react. They'll twirl and dance in spectacular fashion, a dance for the real world alone.

> Similar compromises can be seen in other fields. For instance, SpaceX uses Methane in their Raptor engines for a number of reasons, including efficiency, etc. However, a significant benefit can be found in combustion simulation. 'cut' fuels like the Merlin's RP-1 fuel undergo thousands of forward and reverse sub-reactions between all the myriad hydrocarbon species that comprise it. With moderate-performance engines like the Merlin, these small-scale effects are apparently less critical. Using a simple fuel like methane allows much simpler, more accurate simulation.

However, the 3D stencils we've used so far can be abstracted into the fourth dimension. We can discretize in 4D, where our mesh contains all time states of all spacial mesh points, and apply the stencils to this much larger set of points.

Unfortunately, these meshes grow as N^4, so FDTD methods are stupendously computationally expensive. Plus, more arithmetic is required at each point.

#### Wavelet methods

One of the more interesting papers is the Wavelet+CG solver.

### Relativistic effects

There are several aspects that simplify this problem. Wakefield solvers such as FBPIC must contend with the relativistic effects that are introduced at high particle speeds; we can neglect these issues entirely.

BigDFT, gprMax, hard to apply boundaries

#### History

The first cathode-ray tubes were in use decades before computing power became sufficient for any of these techniques. These were often designed using electrolytic tank analogs (Staggs, 1965), which mechanically move a probe in a tank of conductive liquid.

In 1977, for instance, [] described using taut wires excited by RF to measure the field. 

Of course, computing all space around the beam seems ridiculous. Many beam solvers restrict their 

SLPIC

There are two ways to implement this: either as a

It is important that the restriction and prolongation operators be mirror images of each other.

For instance, the standard 7-point stencil used in 

<http://viennacl.sourceforge.net/viennacl-benchmarks-amg.html>

5.5 Transfer of boundary residuals

For more, see *An Introduction to
the Conjugate Gradient Method
Without the Agonizing Pain*, Shewchuk et al.

FPGA miners

### Data structures

In general, data structures seem to be about finding a balance between efficiently representing the object and the computational complexity of accessing the data.

As discussed in field solver, 

Fully unstructured meshes sit on one end of the scale. An unstructured mesh can conform itself perfectly to the geometry at hand, requiring few points to build an accurate model.

However, actually operating with this data requires an exhaustive search for neighbors, position lookups, etc. 

In contrast, indexing neighbors in a fully structured mesh requires nothing more than i+1. 

Unstructured meshes (tetrahedral) are usually used for finite-element / finite-volume methods, but can also be used for finite-difference [].

The 'nested' data structures are particularly interesting because multigrid happens naturally.

The author now wishes to bring certain mistakes to attention.

- Irrational attachment to ineffective solutions.

  After the performance of the CPU and cluster was exhausted, alternative computing solutions were sought.

  Initial estimates showed that FPGAs would be 

  It is important to be committed to a problem, of course, for the detached researcher's attention may wander and the solutions they produce become substandard. However, it is important that any specific solution be abandoned if fundamental flaws are found, and that the chosen course of action be continuously reexamined.

  The fact that the DOD has recently replaced almost all FPGAs wholesale with GPGPUs should have hinted at their effectiveness.

- Misunderstanding of base concepts.

  Residual tweet.

- Mindless 'cycling' through the solution space.

  At a ce

- A single analytic expression can tell you far more about the nature of a problem than countless simulations.

  Test

#### Magnetic fields aren't useful for this problem.

After many trials with IBSimu, I discovered beam rigidity.

> Lesson learned:
>
> A single analytical equation, no matter how oversimplified its description of reality may be, can provide a tremendous amount of understanding about the *character* of a problem.
>
> <https://blogs.sciencemag.org/pipeline/archives/2019/11/13/simulation-and-understanding> Simulation is not understanding.

#### Lessons learned:

- *Briggs' Multigrid* has a wonderful section on troubleshooting codes. 

  -   Visualize the output. With high-dimensional codes, it's easy to miss a corner test case; inspecting the mesh by eye can make issues obvious. 

- Practice the algorithms you're going to implement. Get a feel for how they behave, what sort of convergence and timing you can expect. Jumping to a full-size 16M-DOF problem in 3D in a nonlinear language like OpenCL without first getting an intuition as to how these techniques operate was not a great idea. 

  For one, all the operators are become fiendishly complex as dimensionality increases, making it easier to make silly mistakes. The test cycle time of larger problems becomes huge, and waiting for GPU setup fills, kernel compilation times, etc.

  An unfamiliar algorithm should be gradually prototyped, first in 1D in as high-level a language as possible, then in 2D with some added complexity, then in 3D. At this point, you should have a slow but complete reference implementation from which you can develop a fast one.

  As horrifying as it may sound, TDD seemed to be beyond useless during this project. The complexity of the functions were not sufficient to demand it, and requirements changed too quickly. The whole API would be re-written hourly, data structures would change as performance issues became apparent, etc. It may be helpful to pause test coverage while prototyping.

  Note also that the character of many algorithms can change drastically as the problem size increases. 

  Premature optimization isn't necessarily the root of all evil in scientific computation. 

  Visualize

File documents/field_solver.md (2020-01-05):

#### Hubris note

T

Particle-in-cell codes all have one thing in common: they require the electric field to be known in some volume of space. 

There are a few ways that one could do this. 

#### Meshless methods

Methods exist to solve Green's function. 

These aren't 

The really fantastic thing is that both heat transfer, electrostatics in dielectrics, and magnetostatics  share the same mathematical relationships; so once we find a solution for one, 

The definition of the derivative

Say we've got some arbitrary arrangement of electrodes with specific voltages, and now we'd like to know what the force would be on some particles nearby. Well, the force on a particle is proportional to $\frac{voltage}{distance}$, so we need the voltage potential field.

This is Poisson's equation. 

$$
\nabla \cdotp \nabla\phi = \frac{q}{\epsilon_0}
$$

This may look quite daunting to the uninitiated, but rest assured that after we do away with notation, the concepts involved are very simple.

$\phi$ (phi) refers to the potential field. Taking $\nabla \phi$ (the gradient of the potential field) means asking "which way is uphill, and how steep is it?". If a ball placed at a point on $\phi$  wouldn't roll, $|\nabla \phi| = 0$. [^1]

$\nabla \cdotp$ (the divergence of the gradient) 

Div 

The electrostatic field has the following intuitive properties: 

- the potential is always smooth, except when forced otherwise by electrodes, and
- always decreasing towards zero, except when forced otherwise by electrodes or space charge.

You may find that this makes intuitive sense - it'd be pretty weird if the field jumped around in the middle of nowhere.

The right-hand-side $\frac{q}{\epsilon_0}$ refers to any charges hanging in the vacuum. This is quite convenient, since we can therefore use this single equation to solve not only the force from the electrode field, but also between free-floating charged particles (the all-important space charge). 

Collisions within a cell (coulomb collisions) have to be handled

It also allows us to find the effects of the particles on the electrodes.

[^2]: You may also hear about the Laplace equation: this is merely Poisson without the right-hand-side, where space charge is assumed to be zero.

Unfortunately, this equation can't simply be worked in the manner you may be used to. So-called 'direct' methods exist, but they become computationally infeasible for more than a few dozen points. 

CG 'updates all values in the direction of a solution'. It requires the matrix to be 'positive definite' - I don't understand what this means, but it distinctly does *not* mean BiCG includes a second subspace for negative definite.

Recall that the potential field must be smooth. What if we took the neighboring points, averaged them, then updated the middle point? This is an iterative solver known as Jacobi. If the new values are updated immediately (such that the adjacent stencils will use the updated value), this is known as a Gauss-Seidel smoother; if the new values are put into a second array, this is a Jacobi smoother.

Many different stencils can be used, from simple 7-point 19-point high-order stencils.

However, there's a problem. Because each point's value depends on each other point, distant corrections will take many thousands of iterations to propagate, causing the convergence to stall. G-S and Jacobi work marvelously for small meshes, but become asymptotically ineffective as convergence progresses. 

--

This is known as Geometric Multigrid. If we do away with the 'stencil' concepts, we can define a more abstract form of the same operations called Algebraic Multigrid. Algebraic multigrid doesn't care about the structure of the data; unfortunately, this means it is typically slower.

$$
\text{T}\phi = \text{F}
$$

In 1-D, that looks like this:

$$
\begin{bmatrix}
       4 & 1 & 0           \\[0.3em]
       1 & 4           & 1 \\[0.3em]
       0           & \frac{5}{6} & \frac{1}{6}
       
     \end{bmatrix}
\begin{bmatrix}
        0           \\[0.3em]
        \frac{1}{6} \\[0.3em]
        \frac{1}{6}
     \end{bmatrix}
= \begin{bmatrix}
       \frac{5}{6} & \frac{1}{6} & 0           \\[0.3em]
       \frac{5}{6} & 0           & \frac{1}{6} \\[0.3em]
       0           & \frac{5}{6} & \frac{1}{6}
     \end{bmatrix}
$$

Or, in a more manageable stencil representation,
$$
\phi[x,y] - \phi[x+1,y] - \phi[x-1,y] - \phi[x,y+1] - \phi[x,y-1] = q/e0
$$

All the complexity 

Now, if we wanted to solve for the field at every possible position in some region, we would need to solve an infinite number of these equations, requiring infinite computing power. Moore's law notwithstanding. Fortunately, we can instead solve a reasonable, representative number of points by discretization. A common rule of thumb is 10 cells across the diameter of a beam.

It is also helpful to define the 'residual'.

$$

$$

This is somewhat like the R^2 value in statistics: it describes how well a certain mesh is described by the equation.

If you just want a fast stopping criteria, you can cheat by subtracting each iteration of the solver from the previous one; the largest difference is a fast stopping criteria on vector processors.

(confusingly, some appear to define the residual backwards, as F-Ab. This is equivalent, it just means the corrections have to be applied with -).

Now, how are electrodes applied to this grid? Simple: the points within the electrode are not updated after a smoothing sweep. Adjacent points still use these boundary values in the arms of their stencils. The residuals must also be zeroed in the boundaries.

Electrode shapes are known as island boundaries. Applying multigrid to island boundaries can become tricky, especially in corners:

You can see that the corner has been lost when restricting to a coarser grid, preventing rapid convergence. There are two ways to fix this:

- A modified boundary restriction (by none other than walt disney studios!) 

- Running a large number of iterations of a smoother on just the outside of the boundaries.

  <https://people.eecs.berkeley.edu/~demmel/cs267/lecture24/lecture24.html>

Gauss-Seidel's convergence rate is far superior to Jacobi for these problems. Unfortunately, 

Jacobi can be accelerated by turning it into Successive Over Relaxation - adding a term between 1 and 2. The ideal term can be exactly calculated, but generally it's just tuned. This can make the solution much less stable.

How do we tell when we're done? Well, we don't know what the true solution is, so there isn't a way to check if our solution is correct. However, we can measure the change in the field after each solver iteration, or take the magnitude of the residual, or the maximum value. 

This isn't foolproof, and there's some contention regarding stopping criteria for numerical methods.

#### Preconditioning

#### Conjugate gradient

The way CG breaks is quite amusing. One step involves dividing by a matrix dotted with its transpose; if the matrix is not diagonally dominant, you divide by zero. BiCGSTAB splits the problem into two triangles, avoiding this issue. It's usually the solver of choice for these sorts of systems.

One can also use "preconditioners" to make the matrix into a form that another solver can handle. This doesn't involve 

This can be 

> The smoother used in the upstroke of the V-Cycle (Algorithm 1, line 11) performs the operations of the smoother
> used for the downstroke (line 4) in reverse order. E.g.,
> if Gauss-Seidel iteration is used, opposite traversal orders
> should be used when descending or ascending the V-Cycle,
> respectively. For Jacobi smoothers, no reversal is necessary
> as the result is independent of the traversal order

#### Multigrid island boundaries

Dirichlet BCs set the value; Neumann BCs set the derivative of the value. (Robin BCs set both the value and its derivative). A Neumann BC might be used in thermal simulations - to force a steady heat flux, for instance. We won't make much use of it in electrostatics, however.

Surrounding the simulation mesh are the wall boundary conditions. For our purposes, these walls are used to simulate the infinite vacuum that envelopes the domain over which we reign; a layer of Dirichlet BC ghost points are added at 0v. It is important that the walls of the simulation not be too close, or else the field will be distorted. To correctly represent 

In other simulation programs, periodic walls are introduced, perhaps to simulate a long self-similar beam-pipe 

Electrodes are variously called "immersed, embedded, or island" boundaries. They interfere with the coarsening 

<https://amrex-codes.github.io/amrex/docs_html/EB_Chapter.html>

[McAdams 2010]: 	"A parallel multigrid Poisson solver for fluids simulation on large grids, McAdams et al. (2010)"

[^1]: || in this case refers to the magnitude or 2-norm - 

#### Determining electrode properties

It's quite useful to know the capacitance and charge on an electrode; not only is this necessary to predict the slew performance of the amplifiers, but the beam modulation detectors function by 

Fortunately, once the electrostatic field is known, determining the charge on an arbitrary shape is a simple matter of applying gauss's law.

This is the integral form of Gauss' law.

surf int  E dot dA = q/e_0

The sum of the electric field / area normal to any closed shape is equal to the enclosed charge.

From this we can determine the capacitance and voltage of the electrodes.

The surface over which all the charge is summed need not be the electrode itself; it can be a box around the electrode.

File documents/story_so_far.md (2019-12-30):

Written January 2019.

At this juncture, it seems useful to write a quick description of what has come so far and discuss some of the more interesting papers a bit more intellibly than the quick notes that have been made thus far. Much of this is written from memory; it is almost certain that things have been left out.

#### The original idea. 

#### The Zinc epoch

Very little that was done at this time is worth mentioning; it was all entirely rubbish science. 

A 

#### Simulation

November 2017.

After hopelessly naive attempts to simulate particles in an n-body mode using the Coulomb equation 

Salom_Meca and Code_Aster. Unfortunatey, their scripting language and documentation was in french.

Elmer is integrated with CAELinux (that is, computer-aided engineering linux) 

The main ionization method at this time looked like ICP. I 

A fellow named Daniel Bondarenko wrote an excellent paper and thesis defense (with co-authors, of course!) on plasma simulation with ElmerFEM:

Engineering design of plasma generation devices using Elmer finite element simulation methods
https://doi.org/10.1016/j.jestch.2016.07.015

He was kind enough to send an extremely nice email, which I'll reproduce here:

```
Hello Daniel,

Sorry for a delayed response. I was conducting the study at a university at the time and the files are most likely still one the hard-drives of the computers there.

I have my own setup now and play with Elmer whenever I have a chance. To be honest, Elmer is strange in terms of simulating plasma, you have to make a lot more assumptions and have a narrower scope in terms of simulating a specific behaviour; what I've done in the university has some limitations and I'm actually more happy that I could conduct an experiment because it has some bearing on reality.

In a nutshell, I don't think it would be a good idea for me to share the files that I have, because I do this stuff for fun and get in some strange rabbit holes with Elmer, which might appear strange to someone just starting out with it. Keep in mind that if you want to simulate a large system with multiple components and have a mid-sized GPU ready to go, then Elmer FEM won't be the best choice, unless you are really well versed both with CUDA and Fortran. Smaller sized systems, both in terms of mesh and the number of boundaries, can be manageable, but then again, keep in mind the very specific assumptions that you are taking with you to the simulation.

On the note of ICP design, I'm guessing that you are probably considering using a microwave RF source so if you are using the friendlier GUI of Elmer consider using the manual and the example for the microwave duct (Tutorial 16: Using VectorHelmholtz module to model wave propagation in bent waveguide). Also, if you specifically need to see the distribution of ionized particles the wiki has an old but good introduction: http://www.elmerfem.org/elmerwiki/index.php/Electrochemistry

I could answer some questions about plasma, if you want, full disclosure though I don't know everything about it. I'm learning something new everyday and at the very least could provide some direction.

Also, consider joining the Elmer FEM community, people there are excellent and smart and respond pretty fast. Try to get familiar with Elmer first though, at least the GUI portion, rookie questions tend to be ignored.

All the best to you in your simulations adventures!

```

Not to foreshadow, but his notes regarding GPU acceleration were particularly salient.

Warp started out as a Fortran code. Documentation was a little sparse; and modules with DSMC. Getting cell potentials was a little trick,

Simulations on the order of 100^3 were carried out.

Due to all sorts of effects (), quantities like total energy, momentum, etc in a PiC simulation can diverge and

Particles within the same cell of a PiC simulation won't feel any force, so 'Coulomb collisions' are usually added in seperately.  

HBM2

Summing up charge on electrode

FBPic

Electron recombination is a relatively slow process. It's what gives rise to the latent glow of fluorescent tubes, the green airglow of the atmosphere, and other pretty glows. A similar process (electron-hole recombination) allows LEDs to produce light.

#### Space charge 

Much of the below is paraphrased from SIMION's explanation

https://simion.com/definition/childs_law.html

SIMION is a general-purpose beam simulator.

$ \nabla \cdot \mathbf {E} ={\frac {\rho }{\varepsilon _{0}}} $

This means 'downwards everywhere' - the field always goes towards zero away from space charges and electrodes. It also means everything should be smooth. 

Poisson's equation:

$ {\displaystyle {\nabla }^{2}\varphi =-{\frac {\rho }{\varepsilon }}.}$

The Child-Langmuir law provides a 1d analytic expression that describes how charged particles can become 'bunched up'.

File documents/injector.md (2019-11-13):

```
"mmworm" injector

| - 12L14 or equivalent, probably passivated?
: - bearing material (optional)
o - copper winding

 |: ooo| *|:|
o|: ==-O>*|:|o
o|: ooo||*|:|o 
o|:____||*|:|o
o|:|      |:|o
 |:|      |:|
 |:|_____ |:|
 
Blade > energized by clamp solenoid on plunger clamps down on wire *
Plunger turned to size then milled radially on CNC in 1 op.

Wire hole should probably be centered so that it can be drilled by a lathe operation.

There could be two or more blades and solenoids per plunger.
Return pressure on both plungers could be effected by spring, or by a second coil.
Wire is fed by sequentially pulsing each solenoid. 
Hard stops should be integrated so that a known length is injected per stroke, and so the clamp plunger sees maximum force.

The clamp plunger could be actuated by the advance solenoid somehow. More complex geometry, probably. Could also be coupled inductively! 

Solenoid wire fatigue is a concern.

It remains to be seen whether the tribology of 12L14 requires a bearing insert - delrin AF, perhaps alumina-alumina, or even a thin graphite layer.

If reversing wire is not required, the two solenoids could simply be connected together and driven simultaneously as long as the inner plunger is faster than the outer.

The two solenoids will have different inductances and resistances etc, perhaps that could be leveraged to control them seperately. 

Clamp could even be passive, just a piece of spring steel or something akin to a strand-jack collet.

```

```
Inductive mmworm

 |: ooo| *|:|
o|: ==-O>*|:|o
o|: ooo||*|:|o
o|:____||*|:|o
o|:oooooo |:|o
 |:|      |:|
 |:oooooo |:|
 
Plunger coils are connected together.
 
The advance field is activated, and plunger travels to stop. Advance field is driven at resonance, plunger remains at stop, clamp activates. Advance field is turned off (or perhaps frequency/duty cycle changed), plunger returns to rest position, clamp slowly deactivates through remnant field.
 
Advantage: no wire fatigue, only 1 mosfet required
```

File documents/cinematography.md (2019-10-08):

Oh, and it costs the same as a first generation Makerbot Cupcake. That was made out of wood.

How is this possible? 

beat

Uh... we've got a device that can produce arbitrary geometries out of almost any material

[closeup, ceramic pcb blinking with STM32]

This is a printed circuit board.

If you look closely, you might notice a few unusual properties.

64 layers, 

[microscope shot]

alumina ceramic substrate.

For one thing, there's no solder; the copper merges with the components - almost as if the board had been built around the ICs somehow. The traces are all thinner and thicker, this one is a vertical smiley face, this switch is actually a DNA double helix, this one just turned into iron,  [gradually more absurd geometries]

also,

[zoom out rapidly, board still blinking]

it's twisted into a mobius strip.

[Hammer smashes it to demonstrate that it is still ceramic]

It's fine, let me make a new one.

[button pressed, printer closeups, timelapse, window visible to show time]

Overlay: 26 minute print: $3.4.

Here's a Borromean teacup. The cup is ceramic lined with copper, and the handle is pure iron.

Dialog: "Today I have to make a thermionic cathode out of rat poison, nail polish, and vape wire. Perhaps unsurprisingly, this process has not been well described in the literature."

A note on customer support:

I think this device is most useful if it's accessible to everyone. The beauty of an entirely novel Unfortunately, due to the complex operating principle, making the nrdditron affordable to hobbyists may be orthogonal with maintaining 1-on-1 customer support, so I can't guarantee the level of customer service that one of the major manufacturers can provide.

Camera that traces the arc of power switch.

Video text overlay "the money I got from my last business is currently on this table." 

BPG400 vacuum gauge  - $90 surplus.

nrditron? Priceless.

gizeh vector animations

http://zulko.github.io/blog/2014/09/20/vector-animations-with-python/

oh ha I'm going to be smiling in the video so one could say I'm "beaming" haha

mixing dialogue with music: https://www.youtube.com/watch?v=fvUn8l30VLc

One of the diffusion pump videos shows me struggling to open a bottle of 704. Might make a good rest 

PCB in profile,

rotate,

get nassault to go over the video 

use lightswitch trick from nassault's new seeds video

"it's even portable!"

[ picnic in middle of the clearing, blanket, wicker basket, bright sun, wide shot, printer beside ]

"er... nice day"

Wright pub scene style rapid vacuum hiss, part removed from chamber 

One of the videos captured recently shows the turbo controller smoking. To make this more clear, I can xor the video with a clip a few seconds before to isolate the smoke.

"Still alive-style" ASCII outro with credits - 3d isometric?

All future improvements will remain open-source. Ideally, any upgrades that are made as the technology progresses will be printable on the device itself, though this may not be possible in some cases.

#### Limitations

There will likely be a few consumables; these print modules will probably require replacement every few thousand hours, or about every 10 kg printed; but there will never be any kind of DRM on those, so other vendors will probably appear. The business model is not predicated on profiting from parts wearing out or planned obsolescence, since that's a dick move; rather, we're selling the device for a reasonable price and then trying to support it as well as possible.

If we profit significantly from replacement parts, there is no motivation for us to improve the reliability of our product. This would be a sad state of affairs.

There will never be any sort of planned obsolescence.

The D in DRM stands for Douchebag

# Focus stack, but nonlinear

Capture many images at different focus positions, and only stack the furthest and closest, for instance.

Fancy bokeh

Split focus

Brenizer Method

wear hat outside at portable

The original Short Circuit intro (<https://www.youtube.com/watch?v=pUQIKnrZVTM>) is entirely close-up macro shots. The camera never moves, it's just a series of jump cuts of motion. The sound is prominent over the music.  The action sequence is 2 minutes long. Everything's slow and methodical; it's clearly distinct from a simple montage.

Nobody is visible; hands are gloved, everything visible is mechanical.

Everything must be third-person scientific; no "I", we, etc

databending/databending - perhaps with ASCII readout of printer startup?

moviepy compositing

<https://gist.github.com/NeuroWinter/e557bfc555118ed68df88e8e51f03177>

There's a scene in 20180111_195750.mp4 where a Q-tip gets sucked into the CNC

> So, I've run up against a bit of a stumbling block. I need to know the electron impact momentum balance of aluminum and copper; that is, when an electron and - say - aluminum particle get in a fiery wreck, which way do each fly off. So I tried to find the predictive theory that governs this, only to find that - to the embarrassment of physicists - it doesn't appear to have been fully developed yet. The best fits available only get within half an order of magnitude. 
>
> The quantum mechanics that fundamentally govern these collisions would take me many years to even begin to understand. 
>
> How about empirical equations? The best ones available 
>
> Somewhat surprisingly, the only experimental data I can find is on electron impact cross section from the 1960s; it seems nobody enjoys putting boiling aluminum into their particle accelerators.
>
> So the only course of action seems to be building a device that can take these measurements. This is a hybrid quartz crystal microbalance, Kelvin cup, and beam calorimeter, all on a nitinol servo. Since plastics, oils, bearings, etc can't be put in a vacuum, we have to 

Camera on winch moves smoothly across the ionprinter deposition chambers, peers beside to where I'm standing, and switches focus to me, beaming. Maybe some split focus magic

Camera switches to 

> So, what is it? Essentially, it's a particle accelerator that builds things. Indeed, many technologies (like the beam position monitors) are borrowed directly from the LHC and lesser accelerators. 

VCR camcorder is upstairs; might be cool for some retro-style effects. Over-recording, perhaps?

'powered by debian, notepad html button'

mdp or tpp or vimdeck closing credits?

This technology has a long and sordid family tree - it's hard to know exactly what to call it.

"this is governed by the Child-Langmuir law, which is essentially the particle accelerator equivalent of a traffic jam"

RF metamaterial with hackrf

'build up' solids in sim animation from corner

Press kit would be really helpful.

Sepia + closeup of keyboard is neat.

Face mask monitor reflection like 2001?

manual tilt-shift by removing lens

Black laptop, no sound, 30 FPS, 1080P, "raw output", USB3 cable in usb2 port, MJPEG camera setting

Video setting 'hardware defaults'. PORTAUDIO internal mic worked, but audio quality quite poor.

Guvcview 2.0.2.

Playing ASCII art video looks really cool

`mplayer -vo aa -monitorpixelaspect 0.5 VID_20180804_125425.mp4`

or 

`mplayer -vo caca VID_20180804_125425.mp4`

```
CACA_GEOMETRY=80x25
```

ffmpeg works too 

using AALIB, one can vary the contrast to great effect. OSD can be removed.

<http://www.mplayerhq.hu/DOCS/HTML/en/aalib.html>

aa:extended works too

Overlay ascii'd video with transparency fade in 

moviepy perhaps

We choose to do these things not because they are easy, but because they're totally rad.

"The pressure in each emitter is only about x Pa, so the part is quite literally formed out of thin air."

potting compound looks pretty cool

An explanation for each sequence could be put in the subtitles, or as an overlay card if it wouldn't be too distracting

30s/40s public-domain swing/jazz for plasma interlude

neutral density filter + washed out background = crisp image through 

This technology exists; it just used to be limited to angstroms per hour, rather than centimeters.

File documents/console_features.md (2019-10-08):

Remotely-updated MOTD with recalls, etc

Integrated model 'package manager' like thingiverse; publish a print recipe with a single command.

Integrated IRC help chatroom? Might distract conversation from the discourse

'Loading screen' scroller is 2d poisson field like cmd-line simulator

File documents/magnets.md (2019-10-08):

Barium Ferrite is a good high-temperature magnet material; good to ~300c, sinterable,  pretty spicy in terms of toxicity.  See <https://patentimages.storage.googleapis.com/b2/26/d8/8714585053693a/US4457851.pdf>

Requires ~10K Oersted magnetizing field; somewhere around 150 kA/m - 750A for a 0.5 cm bit.

Saturation energy product might be a more useful spec; this is 5 to 12 kJ/m^3 for BaFe. (Ormerod and Constantinides 1997). Some hobbyists have made their own magnetizing coils with a big cap. 

Could use a thyristor for triggering.

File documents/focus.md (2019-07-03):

It may behoove you to read a bit of 

> Humphries, Stanley. Charged particle beams. Courier Corporation, 2013.

for some background.

Einzel lenses

Collimation

The ion printer 

*WARNING*: I am confused by ion optics. If you thought I was incompetent before, check out this fuzzy understanding. Everything I say below may be entirely incorrect and based on a totally flawed intuition. 

As far as I can see, the traditional way of doing this is to use something like an electrostatic Einzel lens or magnetic yoke to focus a thick beam down to a point. Schematics of these methods are readily available online. However, you quickly encounter a problem: beam current density and space charge.

To my understanding, each particle in the beam has a charge. When the beam is thick, this poses little issue; the inter-particle forces are negligible, and the beam propagates approximately parallel. However, the tighter you try to focus the beam, the more each particle tries to repel one another. As you increase the beam current density and the number of particles per unit area increases, the distance between them decreases proportionally, and the divergence force increases.

To counteract this effect, you can increase the transverse particle velocity, squishing the beam tighter together. This means increasing the axial particle velocity, requiring more energy.

Since we're trying to move substantial amounts of material, the beam current (charged particles per second) in this ion printer is extremely high - dozens of orders of magnitude higher than even many particle accelerators. So high, the design crashed IBSimu.

IIRC, to attain a dot size of ~50 micrometers, each particle would have to have something around 1 MeV - easily doable with a mini cyclotron or syncrotron. Minor radiation danger, you know, but nothing too serious.

Except for the multi-gigawatt power consumption, the heat dissipation of which would immediately destroy the build platform, along with the printer, the operator, and the building.

This effect is what Feynman referenced way back in his 1969 lecture, "Plenty of Room at the Bottom".

But we have a trick. A glorious, wonderful, magical trick.

#### The trick.

*There is no reason why the beam has to be charged when it converges.*

In other applications, the beam must be charged - often that's the whole point of the beam in the first place, to deliver targeted charged particles or produce secondaries.

But not here. We only care that the particles are in the right place. 

Once the particles are set on their way, we can remove the charge. 

If we can recombine and neutralize the beam before we get anywhere near that tight bit, we elegantly sidestep all these pesky space charge density issues, and our problem becomes delightfully sedate. Since everything's now uncharged, only esoteric weak polar interatomic or Pauli effects remain,  which are surely negligible at these scales.

This, surprisingly, is easy - how this is done is discussed in Hot Cathode.

Optics are confusing. 

Some stream-of-consciousness:

[1] describes vividly how optical systems can't turn a non-collimated beam into a single point due to the conservation of etendue. We can't possibly make a perfectly collimated beam, however we may try; the bowtie orifice must have a non-zero size, and therefore the minimum beam dot size on the target is limited. A bit of playing around with ray-tracing optics programs also seems to confirm this. So, that's it, right? Case closed; the device is impossible.

However, a few moments consideration can falsify this line of thinking. Electron microscopes use tungsten filaments or lanthanum chunks as their electron sources, and yet can resolve details orders of magnitude finer than the source diameter. An early CRT with a cathode aperture size of 0.8mm could form a dot of 0.4mm diameter.

Back to theory.

[3] describes the theory behind CRT optics: it's extremely simple. The minimum dot size is just the distance from the target to the lens divided by the distance from the source to the lens, multiplied by the bowtie orifice size. If we have the print bed located 10mm away from the magnetic lens, set the distance to the bowtie to be 0.5m, and have a 0.5mm bowtie orifice, our minimum feature size will be a perfectly acceptable 10 microns.

This does mean that we'll have a very short distance in which the recombination must occur. The ion curtain will have to have a thin cross-section.

Update, several months on. These problems are aggressively non-linear, and so the precepts of geometric optics no longer hold.

Beam current: 35.757 A 

[1]: https://what-if.xkcd.com/145/
[2]: US Patent 2,825,837, M.D.Dudley, "Electrostatic focusing system".

[3]: http://celco-nj.com/SID_Paper01.htm

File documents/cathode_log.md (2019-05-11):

Using "Mary Kay base coat / top coat" clear nail polish - almost full, 7.5 mL bottle. I am unsure of its precise composition. 

a[^commercial_coatings] describes mixtures of metal carbonates at 22 to 44% W/V. A 30% w/v BaCO3 solution was chosen, requiring the addition of approximately 2.25 grams of BaCO3.

The carbonate did not immediately form a homogenous solution; magnetic stirring was required.

Four Nichrome 80 filaments were wound with 4 turns around a 2.38 mm mandrel: two 24 AWG, and two 32 AWG.

The wire hadn't been cleaned before winding, so the coils were sprayed with IPA. Ultrasonic cleaning would probably have been preferable: if this technique is not found to work, surface contaminants may be the cause.

Two of the coils were dipped in the solution. Two remained uncoated to act as controls.

[^commercial_coatings]: [internal](../references/filament_coatings.pdf)

<hr>

Another strike against barium oxide cathodes: the temperature-resistivity curve for nichrome is pretty funky and surjective, whereas tungsten's curve is quite well-behaved.

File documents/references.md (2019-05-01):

$
%&LaTeX
\documentclass{article}

\usepackage[latin1]{inputenc}
\usepackage[T1]{fontenc}
\usepackage{textcomp}

\begin{document}

\begin{thebibliography}{41}

\bibitem{biondi1949measurement} Biondi, M. A., \& Brown, S. C. (1949). Measurement of electron-ion recombination. \textit{Physical Review}, \textit{76}(11), 1697.

\bibitem{bliss2004evolution} Bliss, D. F. (2004). Evolution and application of the Kyropoulos crystal growth method. \textit{50 years Progress in Crystal Growth}, , 29.

\bibitem{blocher1957carbide} Blocher Jr, J. M., Ish, C. J., Leiter, D. P., Plock, L. F., \& Campbell, I. E. (1957). \textit{Carbide coatings on graphite}. Battelle Memorial Inst., Columbus, Ohio.

\bibitem{cimrman14:_sfepy_write_your_own_fe_applic} Cimrman, R. (2014). SfePy -- Write Your Own FE Application. In P. de Buyl, \& N. Varoquaux (Eds.), \textit{Proceedings of the 6th European Conference on Python in Science (EuroSciPy 2013)} (pp. 65--70).

\bibitem{criado2012ion} Criado, E., Roib{\~A}{\textexclamdown}s, E., Tierno, S. P., Rodr{\~A}-guez De Francisco, P., Domenech-Garret, J. L., Donoso, J. M., et al. (2012). Ion beam neutralization and properties of plasmas from low power ring cusp ion thrusters. \textit{Physics of Plasmas}, \textit{19}(2), 023505.

\bibitem{de2015evaluation} de Oliveira, R. A. {\~A}. {\textcopyright} H., Espenhahn, T., Berger, D., Schultz, L., Ferreira, A. {\~A}.?nio C., \& Stephan, R. M. (2015). Evaluation of linear induction motors with two different topologies by FEM.

\bibitem{dlmf2017digital} Dlmf, N. (2017). Digital Library of Mathematical Functions. \textit{WJ Olver, AB Olde Daalhuis, DW Lozier, BI Schneider, RF Boisvert, CW Clark, BR Miller and BV Saunders, eds}, . Retrieved May 1, 2019, from https://dlmf.nist.gov/19

\bibitem{drela1989xfoil} Drela, M. (1989). XFOIL: An analysis and design system for low Reynolds number airfoils. In \textit{Low Reynolds number aerodynamics} (pp. 1--12). Springer.

\bibitem{erdman1982low} Erdman, P. W., \& Zipf, E. C. (1982). Low-voltage, high-current electron gun. \textit{Review of Scientific Instruments}, \textit{53}(2), 225--227.

\bibitem{mielke1987} Ernest W. Mielke. (1987). Use of Hard Anodized Aluminum for Electrical Isolation. \textit{NASA}, .

\bibitem{goebel2008fundamentals} Goebel, D. M., \& Katz, I. (2008). \textit{Fundamentals of electric propulsion: ion and Hall thrusters} (Vol. 1). John Wiley \& Sons.

\bibitem{gotoh2012neutralization} Gotoh, Y., Tsuji, H., Taguchi, S., Ikeda, K., Kitagawa, T., Ishikawa, J., et al. (2012). Neutralization of space charge on high-current low-energy ion beam by low-energy electrons supplied from silicon based field emitter arrays. In \textit{AIP Conference Proceedings} (Vol. 1496, pp. 368--371).

\bibitem{gwinner2000influence} Gwinner, G., Hoffknecht, A., Bartsch, T., Beutelspacher, M., Ekl{\~A}{\textparagraph}w, N., Glans, P., et al. (2000). Influence of magnetic fields on electron-ion recombination at very low energies. \textit{Physical review letters}, \textit{84}(21), 4822.

\bibitem{halbach2017sparselizard} Halbach, A. (2017). Sparselizard-the user friendly finite element c++ library.

\bibitem{hammond1988brazing} Hammond, J. P., David, S. A., \& Santella, M. L. (1988). Brazing ceramic oxides to metals at low temperatures. \textit{Welding J}, \textit{67}(10), 227--232.

\bibitem{harbaugh1962tungsten} Harbaugh, W. E. (1962). Tungsten, thoriated-tungsten, and thoria emitters. \textit{Electron Tube Design}, , 90--98.

\bibitem{herrmann1951oxide} Herrmann, G., \& Wagener, S. (1951). \textit{The oxide-coated cathode} (Vol. 2). Chapman \& Hall London.

\bibitem{hinterberger2006ion} Hinterberger, F. (2006). Ion optics with electrostatic lenses.

\bibitem{IndrekMandre2007} Indrek Mandre. (2007). \textit{Off-axis electric field of a ring of charge}.

\bibitem{jenkins1969review} Jenkins, R. O. (1969). A review of thermionic cathodes. \textit{Vacuum}, \textit{19}(8), 353--359.

\bibitem{kalvas2014beam} Kalvas, T. (2014). Beam extraction and transport. \textit{arXiv preprint arXiv:1401.3951}, .

\bibitem{kim2005electron} Kim, Y. K., Irikura, K. K., Rudd, M. E., Ali, M. A., Stone, P. M., Chang, J., et al. (2005). Electron-Impact Cross Sections for Ionization and Excitation Database. \textit{NIST.(Accessed 2016) Available at: http://physics. nist. gov/PhysRefData/Ionization/atom_index. html}, . Retrieved May 1, 2019, from https://physics.nist.gov/PhysRefData/Ionization/atom_index.html

\bibitem{kim1983direct} Kim, Y. S., \& Pratt, R. H. (1983). Direct radiative recombination of electrons with atomic ions: Cross sections and rate coefficients. \textit{Physical Review A}, \textit{27}(6), 2913.

\bibitem{lau2001simple} Lau, Y. Y. (2001). Simple theory for the two-dimensional Child-Langmuir law. \textit{Physical review letters}, \textit{87}(27), 278301.

\bibitem{lazic2004influence} Lazic, M. S., Simovic, K., Miskovic-Stankovic, V. B., Jovanic, P., \& Kicevic, D. (2004). The influence of the deposition parameters on the porosity of thin alumina films on steel. \textit{Journal of the Serbian Chemical Society}, \textit{69}(3), 239--249.

\bibitem{lotz1967electron} Lotz, W. (1967). Electron-impact ionization cross-sections and ionization rate coefficients for atoms and ions. \textit{The Astrophysical Journal Supplement Series}, \textit{14}, 207.

\bibitem{lotz1970electron} Lotz, W. (1970). Electron-impact ionization cross-sections for atoms up to Z= 108. \textit{Zeitschrift f{\~A}?r Physik A Hadrons and nuclei}, \textit{232}(2), 101--107.

\bibitem{moshammer1997complete} Moshammer, R., Ullrich, J., Kollmus, H., Schmitt, W., Unverzagt, M., Schmidt-B{\~A}{\textparagraph}cking, H., et al. (1997). Complete momentum balance for single ionization of helium by fast ion impact: Experiment. \textit{Physical Review A}, \textit{56}(2), 1351.

\bibitem{P.M.Roberts/DelphiBrazingConsultants2009} P.M.Roberts/Delphi Brazing Consultants. (2009). Is it possible to braze ceramics?.

\bibitem{perelman1962physics} Perelman, Y. I. (1962). Physics for entertainment.

\bibitem{ponomarevelmer} Ponomarev, P. Elmer FEM Induction Machine Tutorial.

\bibitem{ProfessorD.K.Ghosh} Professor D. K. Ghosh, P. D., I.I.T., Bombay. \textit{Potential \& Potential Energy: Lecture 10: Electromagnetic Theory}.

\bibitem{rashid2011simple} Rashid, M. H. (2011). Simple analytical method to design electrostatic einzel lens. In \textit{DAE Symp. Nucl. Phys.} (Vol. 56, pp. 1132--1133).

\bibitem{seigneur2007laser} Seigneur, F., Fournier, Y., Maeder, T., \& Jacot, J. (2007). Laser soldering of piezoelectric actuator with minimal thermal impact. In \textit{Proceedings, International Conference on Electroceramics (ICE2007), Arusha, Tanzania}.

\bibitem{simpson1963design} Simpson, J. A., \& Kuyatt, C. E. (1963). Design of low voltage electron guns. \textit{Review of Scientific Instruments}, \textit{34}(3), 265--268.

\bibitem{smith1930ionization} Smith, P. T. (1930). The ionization of helium, neon, and argon by electron impact. \textit{Physical Review}, \textit{36}(8), 1293.

\bibitem{TranseneCompanyInc1999} Transene Company Inc. (1999). \textit{Oxide cathode coatings for thermal electron emission}.

\bibitem{kurzweg2012} Ulrich H. Kurzweg. (2012). EVALUATION OF THE COMPLETE ELLIPTIC INTEGRALS BY THE AGM METHOD.

\bibitem{vallette2010analytical} Vallette, A., \& Indelicato, P. (2010). Analytical study of electrostatic ion beam traps. \textit{Physical Review Special Topics-Accelerators and Beams}, \textit{13}(11), 114001.

\bibitem{schroder2012} Weber State University. (2012). Electrostatic Potential by the Relaxation Method.

\bibitem{xu2001low} Xu, S., Ostrikov, K. N., Li, Y., Tsakadze, E. L., \& Jones, I. R. (2001). Low-frequency, high-density, inductively coupled plasma sources: Operation and applications. \textit{Physics of Plasmas}, \textit{8}(5), 2549--2557.

\end{thebibliography}

\end{document}
$

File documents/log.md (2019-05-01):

# Log introduction

#### 1545020962 >

I got out of university today. Let's see if we can get this functional before the next semester starts.

<hr>

Based on last night's progress on the ion beam focus theory, I'm doing some beam simulations with IBSimu to see exactly what kind of magnetic field I'm going to need. 

http://ibsimu.sourceforge.net/examples/analytic_bfield.html

jackson

If you do things just wrong, you get this lovely output. Friggin' Jackson Pollock #4, that's what that is.

Some great info from[^5]

[^5]: Doni, Michele. "Optimization of the ion extraction from an inductively coupled plasma (ICP) by IBSimu modeling." (2013). [Internal](../../references/1545067618.pdf) [External](https://www.politesi.polimi.it/bitstream/10589/81162/3/thesis.pdf)

IBSimu doesn't seem to say anywhere what the bfield units are. I'm assuming they're tesla, since we're running SI and not CGS? To verify, I'm going to check the radius:
$$
r=\frac{mv\sin(\omega)}{qB}
$$
Main beam velocity:
$$
9990.616\text{ m/s}=\sqrt{\frac{2(15eV)}{29\text{ amu}}}
$$

$$
\text{if } B=1\text{ Tesla } r = \text{0.0030 m (3 mm)}
$$

Inconclusive. I can't tell if the path curvature is due to space-charge effects or due to the magnetic field.

https://sourceforge.net/p/ibsimu/mailman/message/28479056/ says SI units are used.

Ah, here we go. Units are definitely Tesla.

null

Here's what we get with no magnetic field, 15eV, 1eV normal and transverse.

1T

 1T field in +Z.

Putting a field in +Y crashes IBSimu.

A KJ magnetics RXC88 magnet has a peak 7T field:ring3.50000-5

7T

<hr>

Acceleration power:

$$
15eV \times 2.232×10^{20}\text{ particles/sec} = 536.4\text{W}
$$

Whew. That's a bunch. 

<hr>
$5.985eV$ will be emitted upon recombination - almost assuredly in the form of a photon with a wavelength of 207nm. That's intense. Probably can't put a window on this thing, though glass and polycarbonate both block almost all  far UV. Have to see if the OD is high enough for safety.

<hr>

Electrostatic focusing seems to be completely ineffective at these high current densities.

no_effect

The LHC's beam current is only around 0.54A. Our beam current will be roughly 66.2 times higher!

<hr>

Oh, if your cylindrical BC is wrong you'll get bad data. Doesn't affect the above.

<hr>
We've got around 7 cm of chamber radius as our maximum focus constraint.

gradient

A 5T gradient just about does it.

Remembered that accelerators use quadrupole and sextupole magnets for focusing. Researching why. 

Man, that is killer. A ~3t field for 0.2+ m. That's going to be tricky to pull off without superconductors. How's the focusing after that?

partial_gradient

full_gradient

Yup, that all makes sense, looks good. Pretty stable at 35.75a of beam current and 15eV. Good stuff.

gradient_30eV

The exact same test at 30eV or 5eV accel. produces identical plots - as expected via analytical methods.

Nulling out the space charge effects doesn't seem to have a large impact on the trajectories. Very strange.

Same for the epot.  

Same even for the bfield. Huh.

Without:

no_scharge_epot

With:

with_scharge

Okay, so there is a slight difference. I guess the scharge effects just aren't big enough yet.

narrow_input

Narrowing the input makes the output wider? Le what? Hmm, might be an artifact of the different magnetic field.

narrow_long

Looks roughly the same. Let's try a lower field with a longer distance to convergence.

no_scharge_long

Yeah, our paths are definitely straight now.

gaussian_2

Using a crude gaussian/gaussian distribution for the magnetic field now. Strange "crossover" effect which remains even if the magnet is moved further away.

loopy

20T may be slightly too strong.

crossover_10t

Yeah, still happening. I'm sure future readers have written me off as an idiot. Oh hey, is the magnetic field being mirrored across the x axis? I'm not sure. 

Let's first get a slightly more accurate magnetic field curtesy FEMM.
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

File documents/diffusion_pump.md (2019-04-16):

### Why diffusion?

Diffusion pumps are simple and cheap, with no moving parts. The alternatives:

* Turbomolecular pumps provide fast pumping rates and low base pressures. My Mk3 test chamber was built around a 20 year old Varian Turbo-V200 turbopump. However, these pumps require intricate, many-stage 5-axis-machined rotors spinning at 50k+ RPM, requiring specialized bearings, high stiffness, and careful design. Presumably achievable, but it seemed like a lot more complexity. My attempts at machining rotors with an electronic indexer failed miserably. 
* Sprengel pumps could be interesting
* Cryotraps aren't practical for this application.

We have to design our own, of course, since even used COTS diffusion pumps cost upwards of $400.

### Nozzle

The design parameters of diffusion pump nozzles have some similarities with rocket engine bells. A series of de Laval nozzles are used to accelerate a gas jet to extreme velocities. The pump will need to operate over a significant range of pressures (naturally); startup will probably occur at around 66 Pa (500 microns), and the system should continue pumping efficiently well past 0.01 mPa.

A solenoid on the nozzle could adjust the profile based on the pressure to increase pumping speed. We'll see.
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

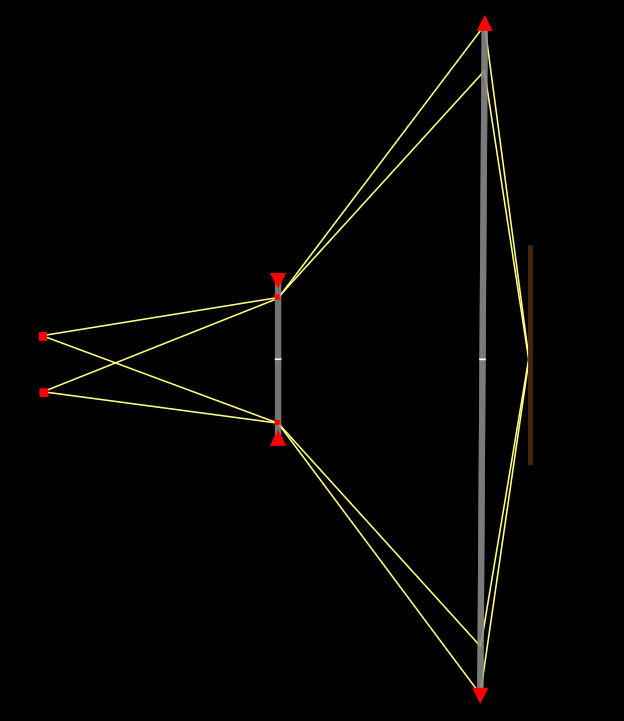
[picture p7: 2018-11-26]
simulation/ray-optics/etendue_5.png

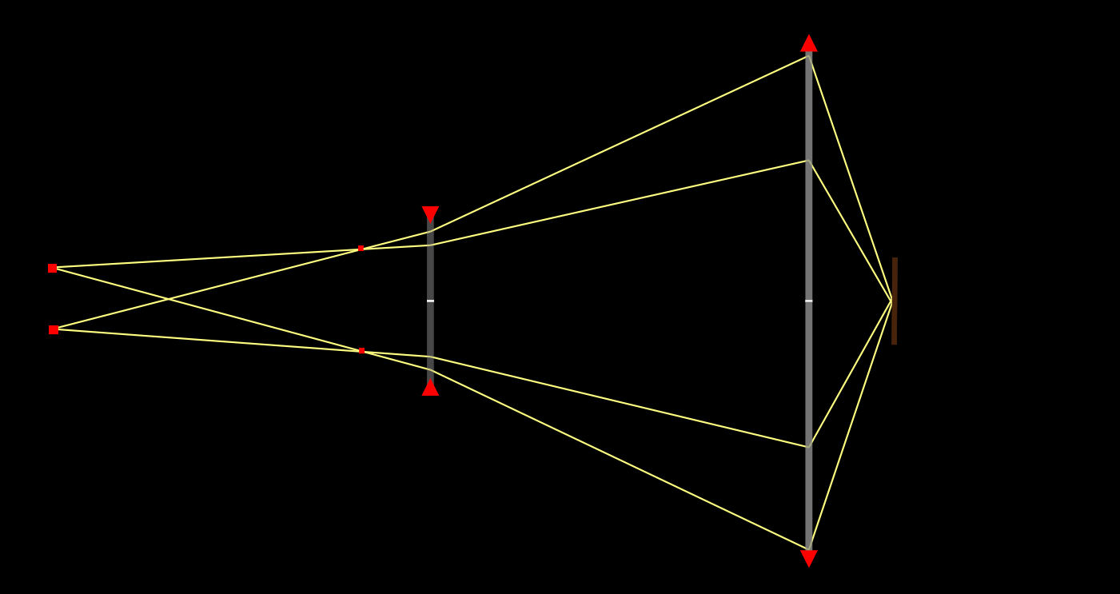
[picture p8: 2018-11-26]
simulation/ray-optics/etendue_1.png

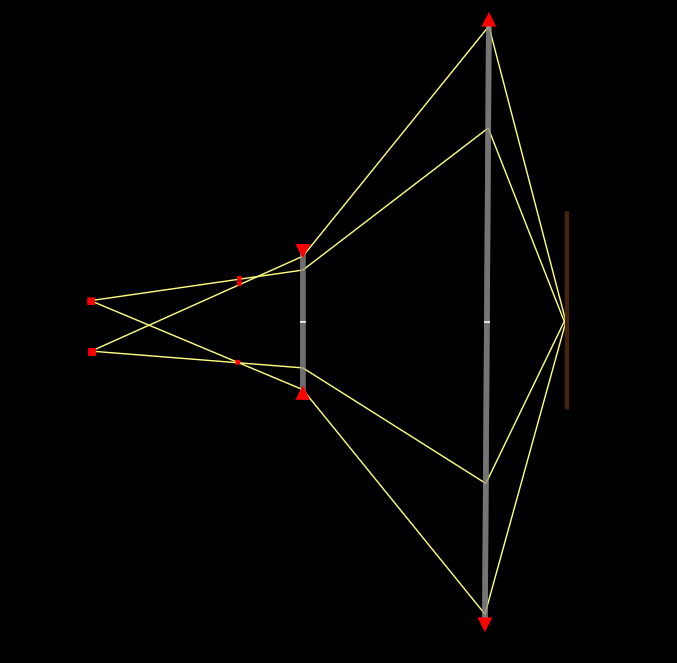
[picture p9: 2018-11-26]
simulation/ray-optics/etendue_3.png

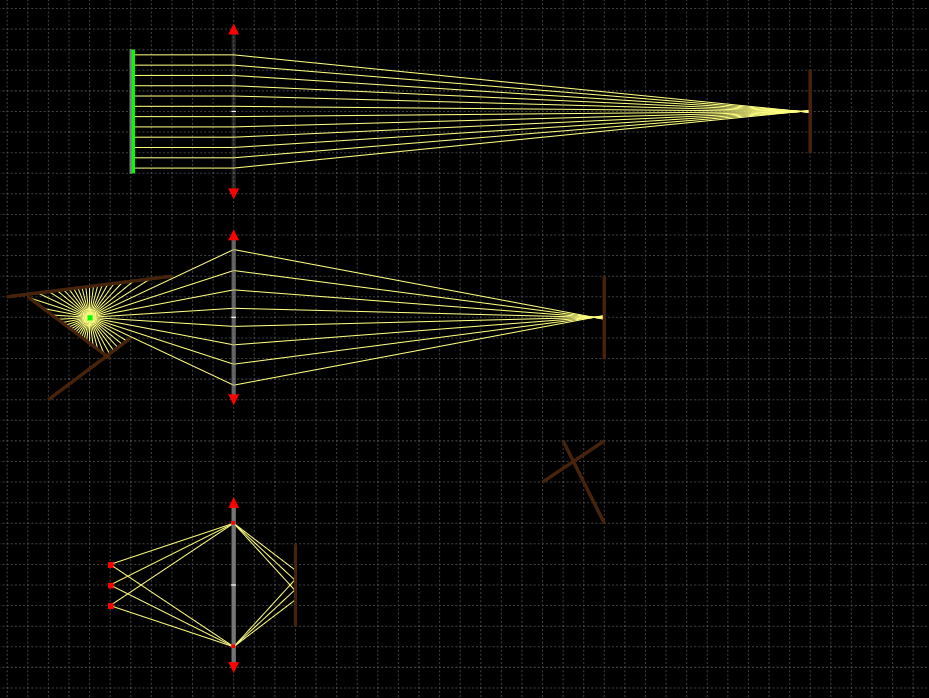
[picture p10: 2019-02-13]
simulation/ray-optics/intuition.png

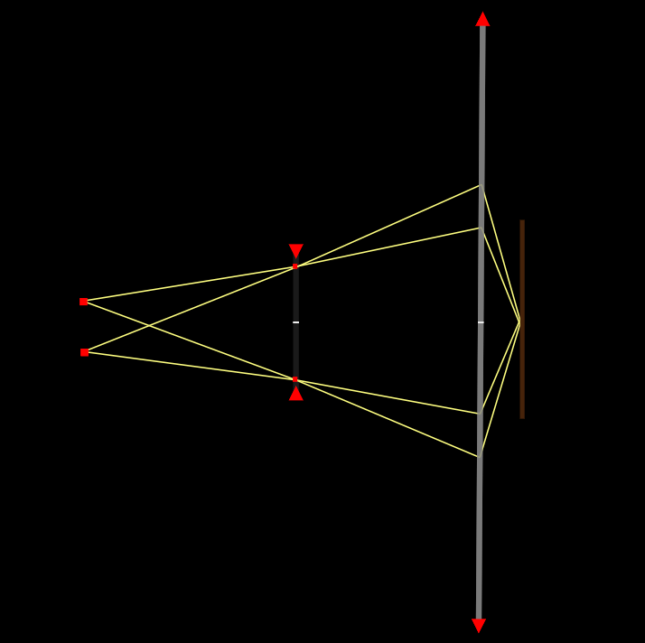
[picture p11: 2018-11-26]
simulation/ray-optics/etendue_4.png

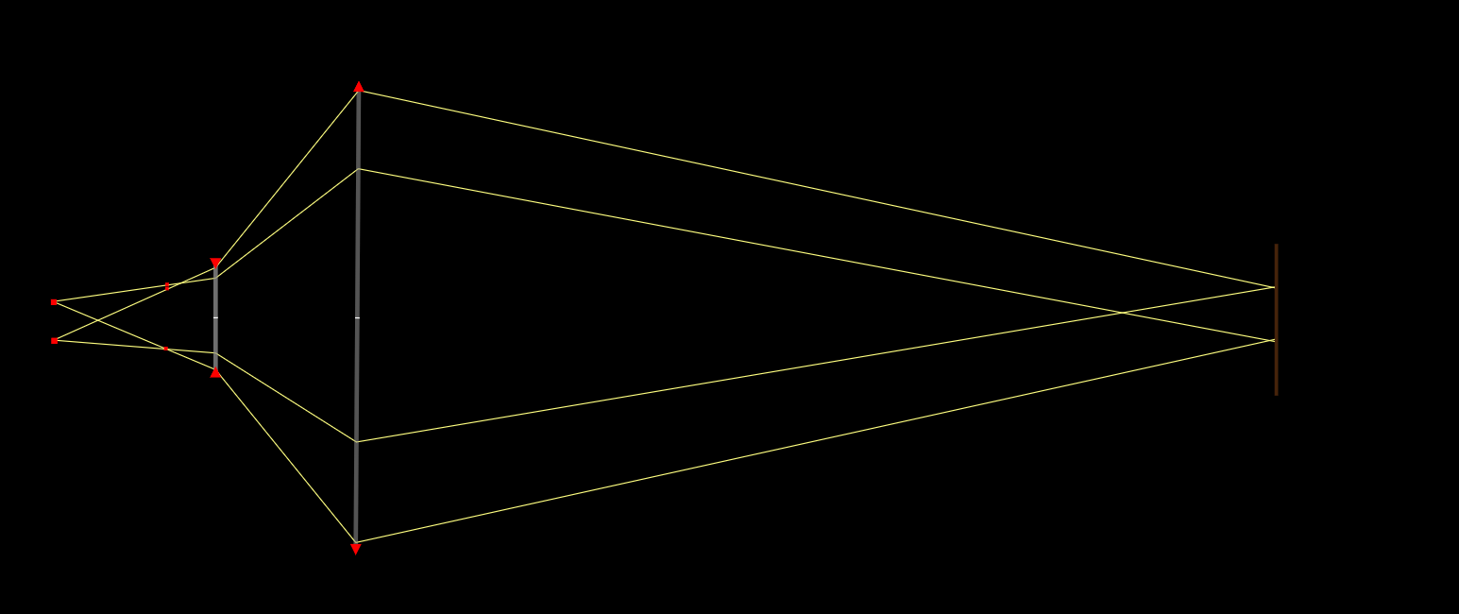
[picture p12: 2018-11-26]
simulation/ray-optics/etendue_2.png

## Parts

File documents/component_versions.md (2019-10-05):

### Prototype

#### Zinc bowtie V1

2016

1. 1/4" copper tubing crimped at one end
2. Coated with a layer of 1400c refractory cement
3. Baked at 60c for a few hours
4. Wrapped with Kanthal A1
5. Coated with another layer of refractory

Boiled zinc effectively, though residual moisture usually

#### Graphite bowtie V1

Resistance was too high; no supply in the lab had sufficient output voltage.

#### Tungsten bowtie tests

1/16" pure (green) W rod

Wrapping alu 

<hr>

### Production

Bowtie R1, serial #s ...

Phased in ... date

process changes go here

should be machine-readable; running command 'list bowtie' or something should print versions and explanations

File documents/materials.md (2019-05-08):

Viton, copper, brass, aluminium, etc.

Polyethylene TML is anywhere between 0.13 and 0.46. Teflon and Rulon are generally >0.01. Viton is considerably higher, at ~0.2%.

Brass is problematic at high temperatures due to zinc outgassing.

Macor is actually surprisingly reasonable. A 1/2" x 3" x 3" block only costs around $60.

UV lamps are recommended for chamber bakeout - thanks Applied Ion!

FR-4 PCBs have surprisingly low outgassing - a full FR-4 stackup has < 0.4% TML and 0.01% CVCM.

Zinc Sulfide is an efficient phosphor.

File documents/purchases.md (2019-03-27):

Aluminum Solder Rods, 2-Pk, Canadian Tire, Aisle 25.

Tungsten Electrode Chemical Sharpener, 5 oz, mcmaster?

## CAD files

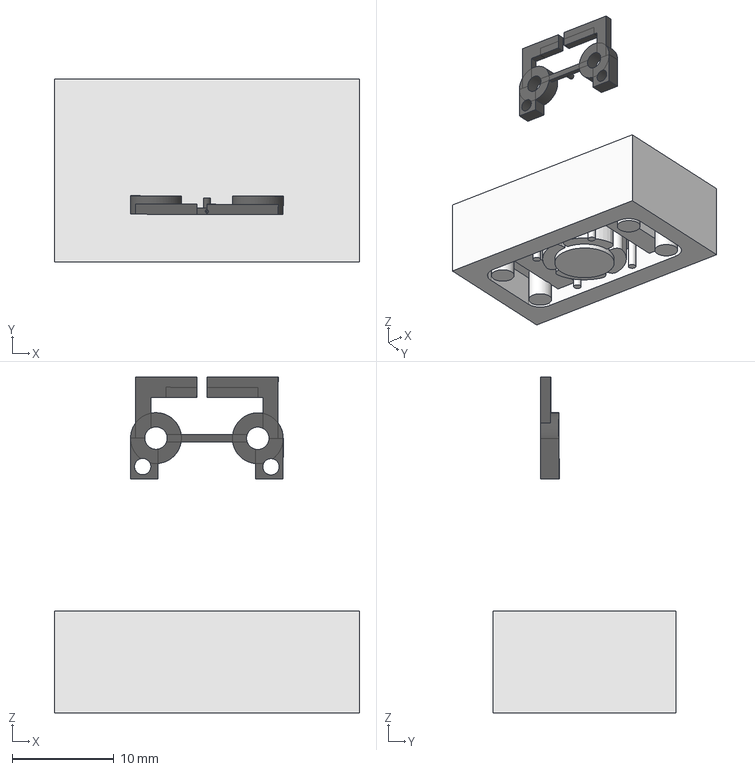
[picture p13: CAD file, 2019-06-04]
mechanical/assembly/assembly.FCStd
30.0 x 18.0 x 33.0 mm

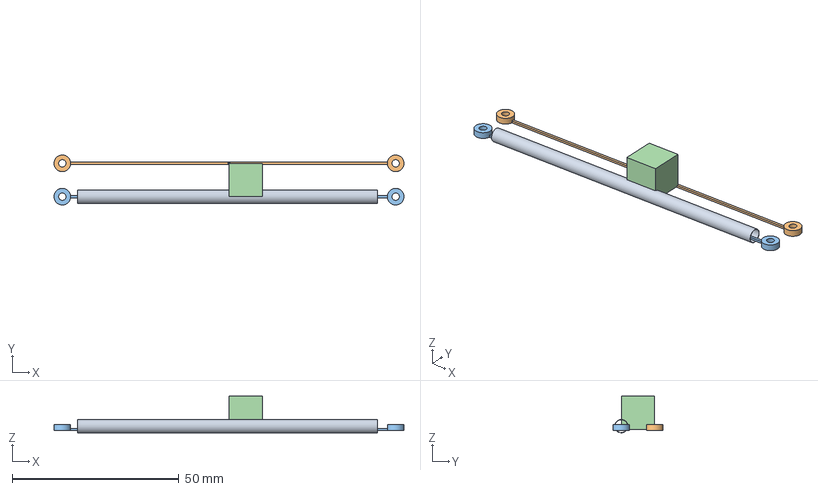
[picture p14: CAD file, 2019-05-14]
mechanical/bowtie/bowtie_prototype_1_looong.FCStd
105.0 x 15.0 x 11.0 mm

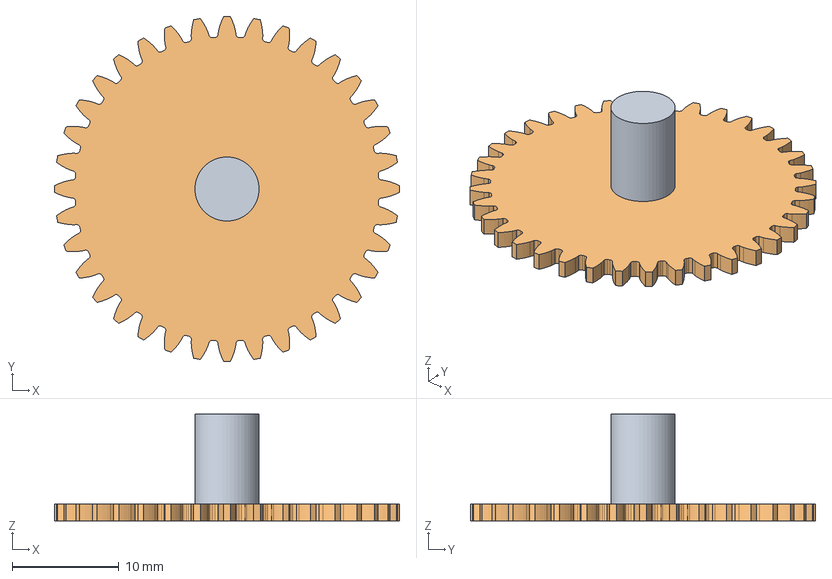
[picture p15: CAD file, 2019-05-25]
mechanical/calorimeter/gear.FCStd
32.3 x 32.3 x 10.0 mm

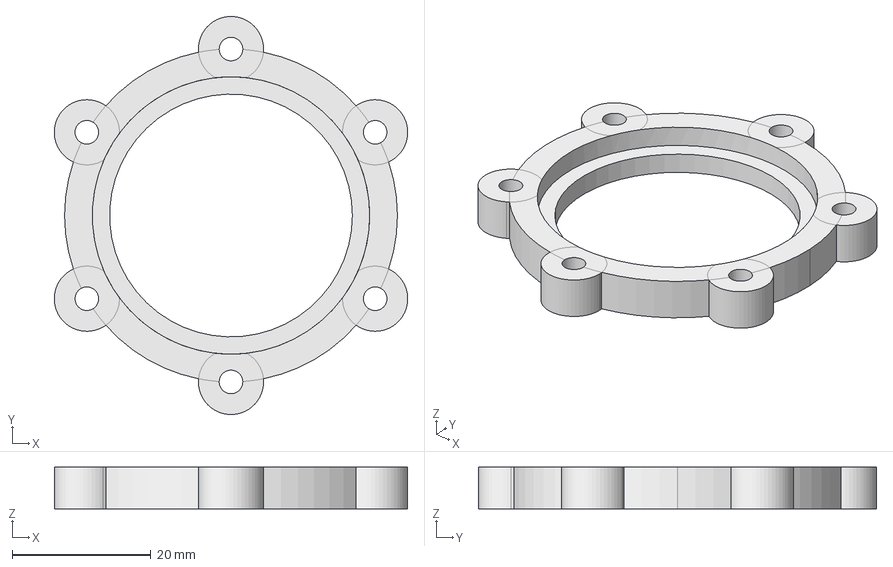
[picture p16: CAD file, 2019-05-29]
mechanical/ceramics_tests/ceramic_holddown_clamp.FCStd
51.0 x 57.4 x 6.00 mm

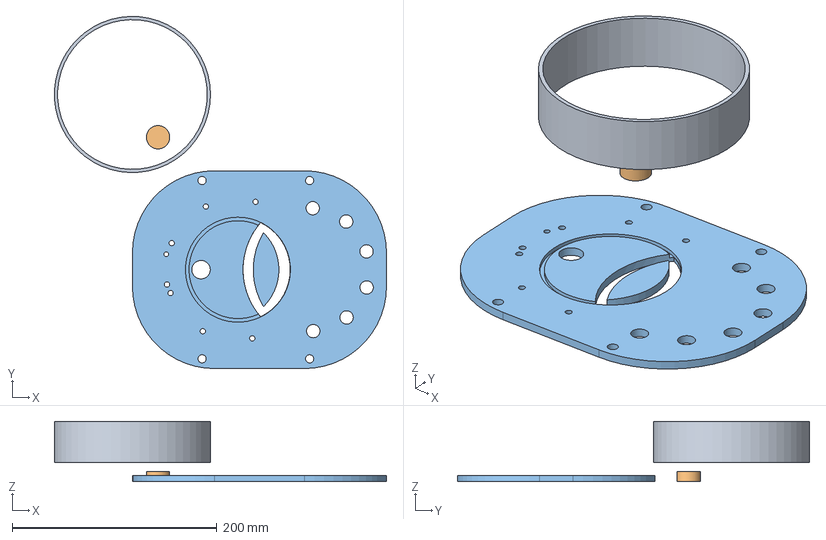
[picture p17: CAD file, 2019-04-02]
mechanical/chamber_plate/mk_3_5.fcstd
324.1 x 343.7 x 59.0 mm
ChamberWall002

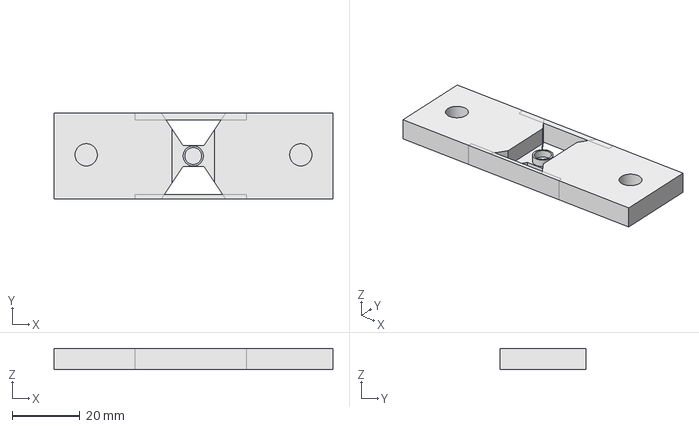
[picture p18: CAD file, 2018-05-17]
mechanical/crucibles/graphite.fcstd
82.5 x 25.4 x 6.35 mm

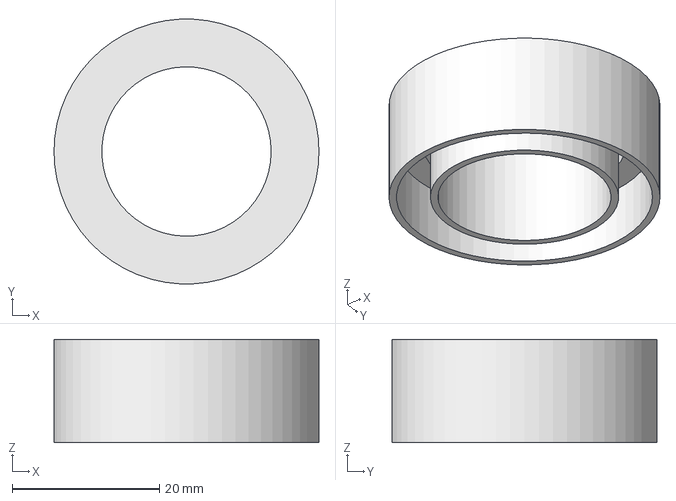
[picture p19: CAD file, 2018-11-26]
mechanical/feedthroughs/FTInsulator1_negative_tall.fcstd
36.0 x 35.9 x 14.0 mm

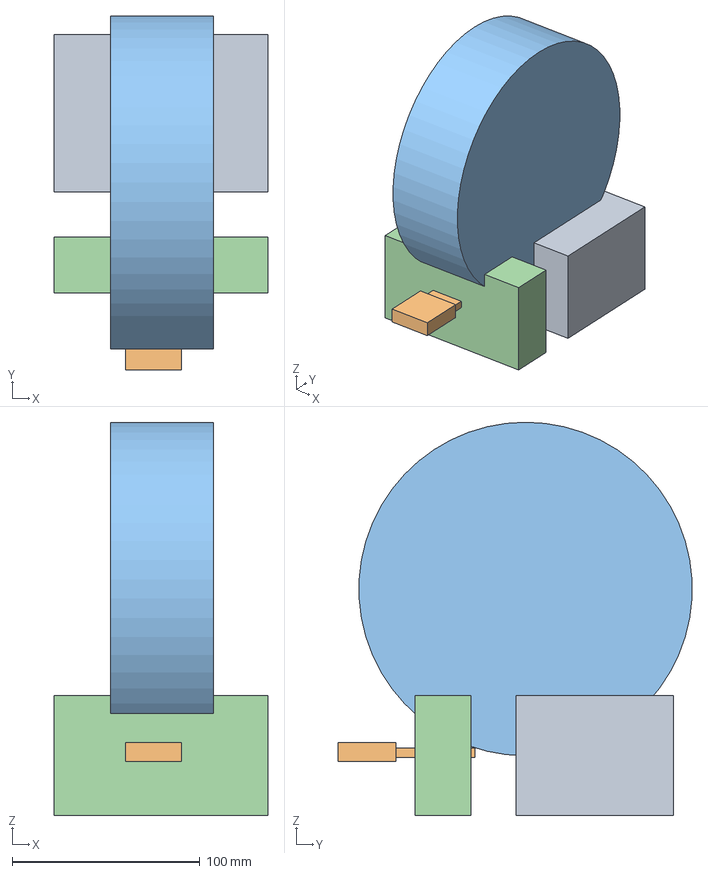
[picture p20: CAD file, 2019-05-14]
mechanical/furnace/blocks.FCStd
114.0 x 188.7 x 209.8 mm
Top
Top001

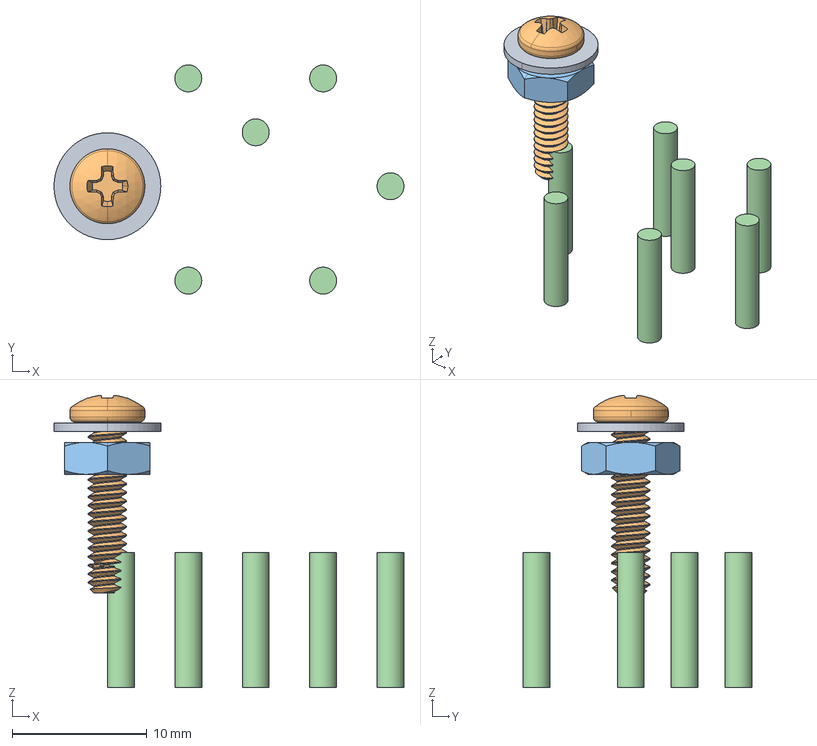
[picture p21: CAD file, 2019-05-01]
mechanical/proto_baseplate.FCStd
26.0 x 17.0 x 21.7 mm
90107A005
91772A110
91841A005

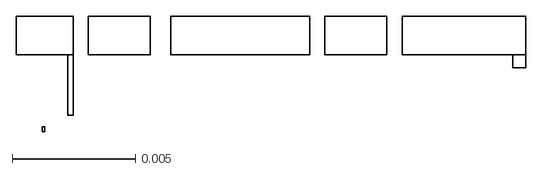
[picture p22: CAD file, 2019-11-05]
simulation/IBSimu/simulations/gui/solid.dxf
0.0206 x 0.00469

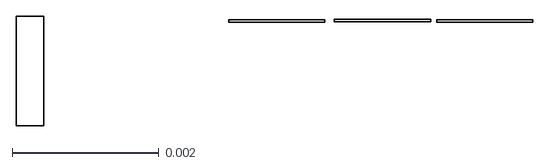
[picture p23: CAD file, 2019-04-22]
simulation/IBSimu/simulations/gui/success/1/solid.dxf
0.00704 x 0.00149

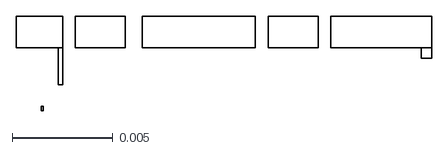
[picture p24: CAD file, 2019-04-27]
simulation/IBSimu/simulations/heavy_beam/solid.dxf
0.0206 x 0.00468

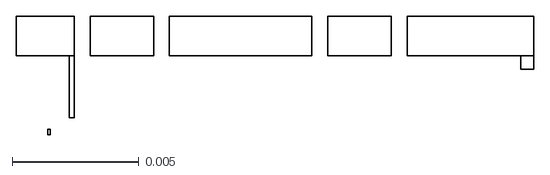
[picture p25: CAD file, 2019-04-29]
simulation/IBSimu/simulations/legun/solid.dxf
0.0204 x 0.00468

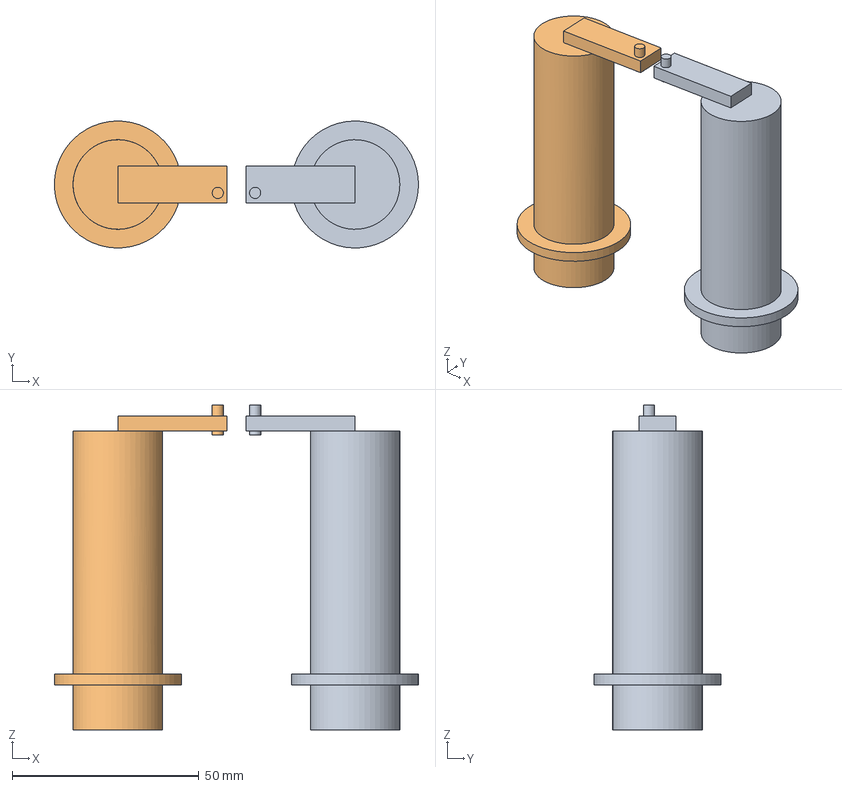
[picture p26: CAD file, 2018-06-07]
simulation/sim_meshes/just_fts.step
97.5 x 34.0 x 87.0 mm

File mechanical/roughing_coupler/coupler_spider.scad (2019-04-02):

$fn=60; 

outer_diameter = 33;
inner_diameter = 18.5;
height = 41;
spoke_depth = 4.3;
spoke_width = 4.6;
difference(){
    difference(){
        difference(){
        cylinder(height*(2/3),d=outer_diameter);
        cylinder(height*(2/3),d=inner_diameter);
        }

        for(angle=[0:45:360]){
            rotate([0,0,angle]){
                translate([(inner_diameter/2)+(spoke_depth/2)-2,0,height/2]){
                    cube([spoke_depth+2,spoke_width,height],center=true);
                }
            }
        }
    }
    
    translate([-1,-1,height*(1/3)]){
        cube([outer_diameter*2,outer_diameter*2,height*(1/3)]);
    }
    rotate([0,0,180]){
        translate([-1,-1,height*(1/3)]){
        cube([outer_diameter*2,outer_diameter*2,height*(1/3)]);
        }
    }
}

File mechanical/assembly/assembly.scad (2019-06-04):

$fs = 0.1;
module round_square(x,y,z,r){
    translate([-x/2,-y/2]){
        hull(){
            translate([r/2,r/2,0]) cylinder(h=z,d=r);
            translate([-(r/2)+x,r/2,0]) cylinder(h=z,d=r);
            translate([(r/2),-(r/2)+y,0]) cylinder(h=z,d=r);
            translate([-(r/2)+x,-(r/2)+y,0]) cylinder(h=z,d=r);
        }
    }
}
module square_hole_pattern(dist,radius,height){
    translate([dist,0,0]) cylinder(h=height,d=radius);
    translate([-dist,0,0]) cylinder(h=height,d=radius);
    translate([dist,0,0]) cylinder(h=height,d=radius);
    translate([dist,0,0]) cylinder(h=height,d=radius);

}


front_plate_height = 4.0;
rod_hole_pattern = 20;
rod_hole_edge_distance = 3;
rod_hole_diameter = 0.1120*25.4;
chamfer_radius = 5;

difference(){
    round_square(25,12,front_plate_height,chamfer_radius);

}

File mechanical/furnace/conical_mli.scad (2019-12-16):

$fn = 30;

CONE_OD_1 = 75;
CONE_OD_2 = 50;

cone_thickness = 0.5;

NUM_CONES  = 3;

cone_height = 115;
cone_gap = 1;

cone_angle = asin(((CONE_OD_1 - CONE_OD_2)/2)/cone_height);
echo(cone_angle);
base_correction = sin(cone_angle)*cone_thickness;

echo(cone_height-NUM_CONES*(cone_thickness+(cone_gap/sin(cone_angle))));


//intersection(){
   // cylinder(h=cone_height-NUM_CONES*(cone_thickness+(cone_gap/sin(cone_angle))),d=CONE_OD_1);
    for(i = [1:NUM_CONES]){
        translate([0,0,-i*(cone_thickness+(cone_gap/sin(cone_angle)))]){
            translate([0,0,cone_height]){cylinder(cone_thickness,d1=CONE_OD_2);}
            difference(){
                
            cylinder(cone_height,d1=CONE_OD_1,d2=CONE_OD_2);
            cylinder(cone_height,d1=CONE_OD_1-cone_thickness,
                                                d2=CONE_OD_2-cone_thickness); 
                                                
            }
        }
    }
//}

translate([0,0,-5]){
    translate([0,0,0]){cube([31.5,12.56,30], center=true);}
    translate([0,0,15+30]){cube([26,6,60], center=true);}
}

translate([0,0,-20]){cylinder(cone_thickness,d1=65);}
translate([0,0,-22]){cylinder(cone_thickness,d1=65);}
translate([0,0,-24]){cylinder(cone_thickness,d1=70);}

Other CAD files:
mechanical/calorimeter/complete_assembly.FCStd
mechanical/assembly/insulator_2.FCStd
mechanical/furnace/cyl-MLI.scad
mechanical/M353-502.stp
mechanical/aluminium_ft_insert.fcstd
mechanical/assembly/insulator.FCStd
mechanical/assembly/pegs.FCStd
mechanical/assembly/pegs.amf
mechanical/bowtie/CER-4.stp
mechanical/bowtie/bowtie_2.fcstd
mechanical/bowtie/bowtie_3.fcstd
mechanical/bowtie/bowtie_3.step
mechanical/bowtie/bowtie_4.fcstd
mechanical/bowtie/bowtie_5.fcstd
mechanical/bowtie/bowtie_prototype_1.FCStd
mechanical/bowtie/bowtie_prototype_1.step
mechanical/bowtie/bowtie_prototype_1_cut.step
mechanical/bowtie/bowtie_prototype_1_milling.FCStd
mechanical/bowtie/bowtie_prototype_1_reflector.step
mechanical/bowtie/nozzle_test.fcstd
mechanical/bowtie/tab.FCStd
mechanical/ceramic_standoff_test_1_cone.fcstd
mechanical/ceramic_wire_feedthroughs.fcstd
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

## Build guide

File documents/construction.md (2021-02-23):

# Mk3

Log starts at gauge.

Need to drill 8.80mm or 11/32 holes in some aluminum and weld with brazing rod.

### Brazing aluminum

Aluminum brazing rod: seems like pre-heating is important. Someone on youtube uses a barbecue to great effect.

Purchased some Benzomatic AL-3 aluminum soldering rods from Canadian Tire. Encountered some difficulty in attaining the required temperature. Melted my jacket in the process.

Tried preheating with an electric stovetop element. The element itself got to nearly 500c, but the aluminum only got to around 300c - below the ~400c required for the AL-3 rods.

Tried oxy-acetalyne, not sufficiently warm.

Tried a 100,000 btu/hr flamethrower: sufficiently warm.

Many voids were found in the final braze - it was not in any way airtight. This may be due to the fact that it was not clamped properly. Re-brazed several times.

Standard table salt is apparently effective as a flux. AvE recommends using a glass rod to remove dross.

Electrochemical weld cleaning

Looks like I put a bit too much heat on the feedthroughs - porosity

Seemed like one of the crush gaskets didn't fully seal on one of the spark plug feedthroughs - but in fact the brazing was porous.

# Mk3-5

Using a scrap piece of aluminum from an old boat engine mount. Had a few holes, but I could work them into the design.

Milled on 6040.

| Tool size | XY feed | Z feed | RPM | Z step | Stepover |
| --- | --- | --- | ----- | --- | --- |
| 1/8" | 7 mm/s | 1 mm/s | 13000 | 1 mm | 50% |
| 0.25" | 11.6 mm/s | 1 mm/s | 13000 | 1 mm | 50% |
| | | | | | |

Vaporized an entire bottle of WD-40 as coolant. This permeated into the MDF spoilboard, gradually reducing the clamping force until the part broke loose. Part was salvageable.

Used an entire pack of 180-grit trying to knock down some of the rack-rash. My friend Arnold tried to flycut  the thing, but there was excessive chatter.

Used an oscillating palm sander with some 320-grit silicon carbide. Took it to a pleasant dull finish.

Cleaned 5 times with water and then isopropyl.

THIS THING looks BAMF.

Spun up a few more times, achieved a base vacuum level of around 0.8 millibar (660 micron) - still not great, but I shut everything down prematurely as heating was excessive.

Set up a liquid cooling system for the turbo.

Purchased some nichrome wire from DashVapes. Needed a driver's license, amusingly.

Quite nervous around this thing right now; the clamping force on the turbo is almost surely insufficient. If it crashes, it will send high-energy shrapnel in all directions, including through my torso. I *like* my torso the way it is, thank you very much.

I raised the input voltage to the turbopump controller to 56v, which worked admirably. The turbo audibly spun up significantly.

Unfortunately, upon re-cycling the chamber, the controller exploded from the excess voltage, presumably spikes due to high startup current. I am unsure as to the cause; the mosfet drivers were clearly blown, but the mosfets themselves were also shorted. The drivers have headroom to 85v, and the mosfets are good to 100v - I can't imagine that switching noise got that high.

Holy crap! The high-side mosfet gate trace and 2 ohm gate resistor blew! That's an incredible failure mode.

Found out why the mosfet gate oxide blew in the first place: the gate was swinging across the entire 50v. Tried increasing the charge pump cap to 0.22 uf , but the driver blew up immediately.

Simplified everything to one channel, same problem. Swapped mosfets, drivers, added an external boostrap diode. Voltage across the diode

I am an ABSOLUTE NINCOMPOOP.  A complete and total kneebiter.

So I tried to determine what caused the tragic loss of my gate oxide. Lo and behold, it seemed that the mosfet gate was swinging the full 48v input, plus 12v from the charge pump.

This is super strange for several reasons: one, the circuit was functioning normally, where the gate should have been destroyed in microseconds;
and two, the block diagram of the MIC4604 driver doesn't reveal a failure mode that could possibly cause this issue.

Cue several hours of anti-Hippocratic probing and prodding that James A. Garfield would have blushed at, and wanton swapping of $40 in drivers

until I realised

it's a *charge pump*, you total f***ing idiot. It's *not ground referenced*.

Floating the board's supply and connecting the scope ground to the drain of the MOSFET revealed a perfect 12v square wave.

<hr>

Spun the pump up again: noise is causing the driver Arduino to reset, which sucks. However, I was able to spin it all the way up; the current visibly dropped from 8a to ~4. The liquid cooling water warmed up quite pleasantly. Capacitors on the driver board warmed up slightly. Only achieved a base vacuum of around 0.7 mBar.

The pump occasionally spins down rapidly when latchup occurs: the energy is being dumped into the mosfets and TVS diode.

Tried using solder to seal up the

Need to cast some crush gaskets.

Wood seems to be an effective mold for solder. Aluminum coated with aquadag or graphite also works.

caulk also works? Huh.

<https://www.youtube.com/watch?v=92OLGmu3hws>

Tried casting lead-free solder in sand: failed miserably, sand melted.

Made a little aluminum mold for a gasket: failed miserably, surface tension of solder was too high.

Tried O-rings to seal, failed miserably, couldn't get below 400 mbar.

Ah, but pure 1101 aluminum wire works perfectly!

Mm, not quite - they were prone to cracking.

Soldered some copper wires into rings - worked slightly better, but still not perfectly.

Ordered in some copper crush washers (#97725A250) from McMaster. These worked well, though a large amount of torque was required to seat them, and I'm not sure how the aluminum threads are holding up. A substantial amount of black residue was deposited onto the surface of the spark plugs from the last attempts. I am unsure of its composition.

Got everything cleaned and polished, washers seated, spark plugs attached - then the second roughing pump coupler exploded.

Designed in openscad, 3D-printing some new ones now.

Printed, installed. Worked fine, except there was a large amount of vibration - might split it into a spider coupling.

Pumped down. Copper sealing rings worked perfectly. It wasn't worth the time to try to make my own.

Hit 5x10^-4 mBar.

Two days later, hit 2.37x10^-5 millibar, even with a few things in the chamber.

second_pulldown

Some discussion on the Vacuum Hackers discord led me to believe that the pump was almost definitely going to fly away, what with the minimal clamping force provided.

Printed out a 122mm bolt circle, disassembled everything, drilled three holes into the table, and re-assembled everything. The pump is now very rigidly affixed via the M6 bolt pattern on the bottom.

Planning on swapping out the buna-n gaskets for viton. Very expensive, but whatever.

Planning on using a few CER-4 standoffs from digikey for the bowtie. These are made of STEATITE C220, with a maximum temperature of 1700c.

Milling graphite; used MeshCAM to generate the features. Went quite well, most broke but one survived. needed G64P.001 to prevent linuxcnc from rounding corners.

Assembled the bowtie module - I'm not actually sure why I'm doing all this, but it went really well in any case.

<hr>

#### E-beam test 1:

4.7 milliamps of e-beam current was drawn with a white-hot 0.1mm tungsten hairpin and a nickel flag at 20v bias. Initial tests with 100v bias were unsuccessful; however, it is believed that this was due to reversed polarity.  

Pressures were stable at 1x10^-5 mbar.

Some tungsten was deposited on surfaces on the chamber; it is assumed that this is due to the unregulated temperature of the filament. As expected, the emission peaked at a certain input power and did not increase further with additional current. The current was increased regardless, and the filament vaporized in a satisfactory manner.

An aluminum baffle was used to prevent debris ingress into the pump.

The pump was accidentally dumped to atmosphere while at operating speed; this does not appear to have caused any damage.

It was expected that beam alignment could be performed manually, by viewing the ion trail left by the electron beam; however, the thermionic cathode produced too much light for this to be possible.

<hr>

A precise reading of the bowtie temperature is now required in order to set the vapor pressure. The resistance of the graphite is an excellent indicator, but the temperature forms a gradient between the center and the mounting points. This gradient has been simulated via ElmerFEM, but ultimately depends on the ceramic interface thermal conductivity etc.

The temperature could also be inferred backwards from the beam current, or by measuring light output.

A thermistor could be used to determine the mount temperature in-situ for a series of power levels, but the thermal mass of a thermistor is likely greater than that of the mount.

Some thermocouple wire was cut to

<hr>

The precise secondary electron energy was at this point unknown. A crude momentum analysis showed a beam deflection angle of some 20 degrees - but this effect is significantly affected by secondary electron energy.

It was decided that a SPARTA simulation would be used to determine the beam deflection; however, DSMC VSS and VHS parameters are required for an accurate picture, and can only be found in

**(Bird94)** G. A. Bird, Molecular Gas Dynamics and the Direct Simulation of Gas Flows, Clarendon Press, Oxford (1994).

A copy of Bird94 was not available online (save for a few pages on Google Books), and a hard copy would cost more than this entire vacuum system. Substituting

<hr>

#### E-beam test 2

A tungsten filament was produced by wrapping 5 0.1mm tungsten wires around each other. The filament was visually aligned with the bowtie.

This filament consumed a whopping 44 watts - while emitting the same 4 milliamps of beam current. Certainly a far cry from the 17w/A figure described in the literature.

As with the last test, this filament saturated the high-voltage power supply. A 31v bias was used instead.

The base pressure attained was significantly higher (2x10^-5 millibar) than in the previous test; this was attributed to the increased clutter within the chamber. Some flux had also splattered.

The charge on the bowtie was measured to determine focusing. Very curiously, the charge increased when the e-beam was activated, but dropped rapidly. This may be an artifact of the relative nature of the measurement, or a symptom of a greater electron-deflection problem.

<hr>

#### ElmerFEM simulations of bowtie prototype 1

The .sif files had been overwritten somehow - reverting to a previous commit fixed the problem.

ElmerFEM requires a .step input. This was meshed with Max h. 0.025 and Min h. 0.001. The enthalpy heat flux was set to zero. Convergence was not well behaved.

The simulation potential was set to 20v, and an ideal temperature of approximately 2000 K was attained. The bowtie drew approximately 100w.

#### Bowtie test 1, 2 and 3

The chamber was pumped down and 10 A was applied across the bowtie. The bowtie glowed a dim red,  not nearly sufficient for deposition. The resistance of the entire assembly was only approximately 0.33 ohms, a significant discrepancy from the predicted 4 ohms. Clearly the graphite resistivity value set in the Elmer sim was incorrect.

The "300-1200v" HV e-beam bias power supply was supplied with 12v, and output 2 kilovolts. A replacement NCH6100HV was purchased.

The bowtie was connected to the 20v-45A supply, and 20a was briefly supplied. Aluminum was readily deposited, and no degradation of the bowtie nozzle was found. The deposited coating was quite easily wiped off the witness microscope slide.

One of the bowtie connection wires melted.

#### IBSimu simulations of entire column

A 3 by 3 by 6 mm 3D simulation was created. Unfortunately, an accurate measurement of space charge requires about 10 grid points across the beam - a mesh of 0.00003mm. This is not reasonable to compute in a short period of time.

However, human factors were encountered - that is, the designer was filled with abject boredom. An automatic solution is required.

#### Beam solver, trial 5

After the modest successes over the previous week, more effort was put into an automatic beam solver.

This was based on the following premise:

1. I am too stupid to design a lens of this sort.
2. I know something about software.
3. Software can design a lens of this sort.

QED.

A mesh of 50x50 pixels over the entire beam would seem to be reasonable.

- 3d "Slice" solver
  - analytic function for slices was not found
- 3d Analytic concentric infinitesimal ring space charge solver, with automatic beam envelope
  - poorly implemented in Python, unusably slow
  - horrific write-only blob of vectors and linear algebra
  - There is precedent for this beam slicing technique, likely quite valuable if correctly implemented
- Brief diversion: an attempt to use TRACE-3D and TRANSPORT to fit the beam
  - miserable failure
  - what
  - what even
- 2d simplified analytic concentric ring space charge solver, predefined beam envelope, rings also used for electrode field
  - Almost usable
  - on the order of a few seconds per iteration in Python
- 2d Laplace + Jacobi relaxation solver for electrode e-field, cylindrical beam scharge using analytic equation from @ Kalvas
  - Simple array operations in Python: 1-2 seconds
  - Numpy convolution: ~0.15 seconds
  - Pretty diagnostics with matplotlib
  - Random search ineffective, genetic algorithm considered with DEAP
  - An attempt was made at adding charge incrementally to obtain a specified gradient - successful for a single point, but not beyond
- Wonderfully fast C++ Laplace solver
  - 24 ms per iteration!
  - aww yis

The search space of possible lens arrangements spans a triple-digit exponent of combinations, so an exhaustive search is clearly not possible. However, seeding the system with some common extraction and focusing arrangements (Pierce, Wehnelt, Einzel, etc) greatly reduces the complexity of the problem.

#### Low-voltage, high-current electron gun, Peter W. Erdman and Edward C. Zipf

and

#### Design of Low Voltage Electron Guns, J. AROL SIMPSON AND C. E. KUYATT

This is the breakthrough I've been hoping for. An e-beam gun capable of ~1-3 mA at 100 eV.

Moreover, simulations (and, indeed, basic Child-Langmuir expressions) have shown that a comparatively high extraction voltage is required to form a reasonable beam. I previously dismissed this technique; my malformed intuition

> There is a general technique which can be used to circumvent these limits on unipotential guns. The technique is to multistage the gun; i.e., utilize a higher voltage to overcome the space charge in front of the cathode and then decelerate to the required final energy.
>
> This technique seems to have first been arrived at on empirical grounds.
>
> Once the advantages of multiple staging are recognized,
> the problem of low voltage gun design breaks easily into
> two parts: the extraction stage and the deceleration stage.
> These designs can be done almost independently and can
> make use of time-proven electron optical elements.

Amazing.

I still haven't been able to fully wrap my head around the energy dynamics of these devices.

Let's draw a diagram.

```
E-beam:

~0.2 eV Emission                                                           /\
----------------                            100 eV Exit                  'o  |
                \                        --------------              -----   
                  \                      /                                  Hapless victim
                      \             ___/                                       Tree
                        \--------/
            ~500 eV Extraction       Focussing, Deceleration
```

That seems quite sensible. If one were to roll a ball down this mount improbable, an observer by the tree would only be struck with 100 eV.

Intuition still rejects this, however. Consider the following: if the second half of the electron gun vanishes, the thoughtful vacuum scientist will have at hand only a 500 eV beam and a shocked expression. If a small plate is surreptitiously inserted centrally, will it not be heated by 0.003 mA * 500 eV = 1.5 W ?  

But then intuition is but a manifestation of a poorly adapted primate, and can only guide one so far in matters of science. I am missing something critical.

In any case, I then simulated this arrangement with IBSimu. Worked admirably - some minor tweaking required, but nothing serious.

beam

diags

#### Erdman-Zipf gun construction

A 1/4" end mill was used to drill the central features - a slight discrepancy from Erdman and Zipf's design, but simulations did not show any effect.

As the mini-lathe used did not have an adjustable tool post, a parting tool holder was ground down to fit.

Machining from a 1/2" stock of copper was attempted; however, the lathe in question (or, more likely, the technique of the machinist) was not capable of machining to any reasonable surface. One particularly aggressive parting operation even caused the fuse to blow.

The copper was exchanged for 360 free-machining brass, and the parts were turned to within ~0.3 mm tolerances. Mill-turning using the CNC would be ideal for rapid prototyping and iteration.

The zinc content of the brass was quite worrying, especially since the extractor will sit ~0.2 mm away from a tungsten wire at some 2000 K. Nickel was therefore electroplated onto the electrodes. The solution drew between 0.05 and 0.1a.

Discussion on Vacuum Hackers indicated that outgassing would be excessive. This idea was abandoned.

12L14 was found to machine quite well on this lathe; however, lead outgassing may be a concern.

Brief diversion to ceramics: On a whim, tried pressing alumina with crude graphite dies. Not effective. Applying small amount of pure alumina to graphite also not effective. Mixed some gelatine and alumina in some random ratio, and applied to tungsten on a whim. Heated with propane torch. The gel-cast bakeoff was very clear and visible - really amazing.

The 12L14 die corroded almost immediately. This effect has been referenced previously as one of the main shortcomings of leaded

After ~6 months and likely several thousand tests, I can say the following with uncharacteristic confidence:

Al2O3 is a BASTARD. It lures you hither with tales of insulating properties, of wonderous high temperatures

There is aluminum dust everywhere

#### The hunt

A search was carried out in an attempt to find an insulating coating or electrodeposition technique that could be used for a few purposes:

- as insulator for electrostatic lens elements, required immediately
- to decrease bowtie emissivity (and, potentially, reactivity) without switching to EDM tungsten

Anodized aluminum could be used - many vacuum tubes have cathodes insulated by aluminum oxide. However, this is slow.

Water glass may also be an option

Things I know how to do:

- electroplate with copper
- electroplate with nickel

- Can nickel be passivated?

- Some nitride? Nickel nitride?

- Silica coating graphite seems to exist

- Iron/steel passivation or pickling could be used

- Anodization of aluminum with mere vinegar has been mentioned once or twice.

- Graphite can be copper plated.

- Copper can be "calorized" - a layer of alumina is applied, which then reacts to form copper aluminate and a coating of alumina. Promising method. Little can be found in the literature about this.

<http://tallmantechnologies.ca/iron-making.php>

> Calorizing is a pack diffusion process where the copper tuyere is placed in a sealed retort containing aluminum powder. The casting is heated and aluminum is diffused into the surface, creating a copper aluminide inner layer and an aluminum oxide outer layer.
>
> Calorizing creates a protective layer on the copper tuyere that preventing liquid iron drips from penetrating the surface. The calorizing process is performed at the final stage of production after the tuyere is finished machined and hardfacing alloys are applied. Calorizing eliminates the need to use refractory materials on the top surface of the tuyere.

- io9 on twitter (thanks!) informed me of the the field-assisted sintering technique, which greatly reduces alumina sintering temperature requirements.

US4418097A

> The present invention comprises a process for reducing high temperature oxidation of graphite electrodes by coating the electrodes with a siloxane fluid.

> Dimethylpolysiloxane, having 100 centistokes viscosity, was sprayed on a graphite electrode while the electrode was at ambient temperature. The electrode was then heated to 1400° F. for eight hours. Weight loss was 6.8%.

Oh wait! That's silicone oil - PMDS!

A bootstrap paradox is found here. All of these techniques will be trivial when the ion printer is functional, but it can't be built without one.

#### SiC Graphite / SiO2

A small sample of graphite was accidentally dropped into a test tube containing a small quantity of ECO-702 silicone fluid. This coupon was then heated with a propane torch. The fluid burst into flames, and produced a bluish deposit on the graphite which immediately flaked off. An inert atmosphere may be required.

One face of the graphite was cleaned, then heated cherry-red and dropped into the siloxane. Some momentary bubbling was observed. The sample appeared to change texture somewhat, and emerged perfectly clean. The sample was still conductive.

Promising method, however.

Silicon Carbide has an emissivity close to that of graphite, so this technique will be useless for decreasing power consumption.

See @ blocher1957carbide for a comprehensive treatment of this treatment.

#### Alumina Cataphoresis

<https://www.thevalvepage.com/valvetek/heater/heater.htm>

> Cataphoresis or electrophoresis is defined as "the migration of coloidal particles under the influence of an electrical potential". Cataphoresis, as applied to heater coatings, is the process by which positively charged alumina particles are deposited on a negatively charged tungsten heater wire. The alumina used in the suspension consists of very fine particles, usually in the one-to-five micron size range. An increased number of ionised groups on the alumina surface results when the particles are surface charged by the addition of small amounts of selected soluble inorganic salts, such as aluminum nitrate.

> After the heater is coated, it is sintered at 1600C for a short time in a hydrogen-atmosphere furnace.

This process was attempted with graphite at 20v, no effect. Experiment was repeated at 500v, no effect. Solution was very dilute - agitation likely required. See @ lazic2004influence for parameters.

#### Bowtie temperature measurement

Precise print speed measurement (that is, atoms deposited per second) is essential to the accuracy of this concept.

There exist some thermocouples A program called LPUWS was found. <https://lpuws.scot.sk/> The endoscope from the PnP machine was removed and connected to a pocket spectrometer; however, the resolution was inadequate. A source of a reference calibration spectrum is unknown. A laser or LED of a specified wavelength may be effective.

The bowtie temperature would be useful to determine the vapor pressure (and thus atoms emitted) of the deposition species. On second thought, the pressure in the nozzle depends on a choked-flow parameter, since the external pressure is essentially zero. Relying on temperature to determine print speed.

However, there are many options for print speed feedback. Trace light emissions from ionization, e-beam current attenuation, etc.

#### Aluminum anodizing

<http://www.observationsblog.com/sciencetechnologyexperiments/anodizing-and-dying-aluminum-without-battery-acid>

"Hard" or "type 3" anodization appears to be desirable for high-voltage applications.

See @ mielke1987 for the breakdown voltages of various thicknesses - >2500v appears to be difficult to achieve.

Bath is generally refrigerated.

<https://www.precisioncoating.com/hardcoat-anodizing-type-iii/>

> "Sanford Low Voltage" process
>
> High voltage rectification normally requires > 30 Amps per square foot current density.
>
>  Dielectric barrier usually > 1000 < 2000 Volt DC.
>
> Hard coat applications require up to 75 V at 24–40 asf.

A suitable boost converter was purchased.

####

The Steacie Library at York U has a shelf (QC 702 onward) with plasma physics books.

"The Physics and Technology of Ion Sources" was particularly helpful.

####

It may pay to re-evaluate the reasoning behind the use of wire stock. Intuition says granular jamming will be a concern, but perhaps some sort of ultrasonic vibratory system could be used to prevent sticktion.

#### Emissivity difficulty

It was discovered that the emissivity of tungsten varies significantly with temperature, starting from 0.05 at 250 K to approximately 0.16 at 1500 K. With 2048 bowties, the

An aluminum reflector could be used - however, thermal heating is a little counterintuitive. For instance, an isolated, completely enclosed object will eventually reach precisely the same temperature as its surroundings. Some simulations are in order to determine what reflector arrangement will be effective.

<http://web.mit.edu/16.unified/www/FALL/thermodynamics/notes/node134.html>

<http://hedhme.com/content_map/?link_id=22144&article_id=530>

<https://nvlpubs.nist.gov/nistpubs/bulletin/14/nbsbulletinv14n1p115_A2b.pdf>

Describes in fascinating detail how the inner surfaces of a tungsten helix filament are significantly hotter than the outer ones.

A bowtie with a reflector was designed and imported into Elmer; however, the elmer mesh generator doesn't currently support multiple bodies.

gmsh was used to mesh the combined part.

`ElmerGrid 14 2`

was used to import the combined mesh (14 is the gmsh format and 2 is elmersolver mesh output) - however, the reflector was not imported. Elmer also crashed. ElmerGrid -autoclean resolved the error.

Apparently only the gmsh "netgen" command can be used with multiple bodies.

The final workflow was as follows:

```
Copy .sif file
ElmerGUI -> Import project (overwrites .sif)
Revert .sif
Export each body to seperate .step files
Import .step files into gmsh, mesh -> 3D, refine (netgen) -> save
ElmerGrid 14 2 bowtie_prototype_1_cut.msh bowtie -autoclean -bulktype 1 1 1
ElmerGrid 14 2 bowtie_prototype_1_reflector.msh reflector -autoclean -bulktype 1 1 2
ElmerGrid 2 2 bowtie_prototype_1_reflector -in bowtie_prototype_1_cut -out finalmesh -unite -merge 1.0e-10
ElmerGUI -> import mesh
Set body numbers using the shell script (and set count in brackets!)
Run
...
Profit!
```

If something in viewfactors.dat breaks, it may be helpful to delete the file. This was required when switching to diffuse gray.

reflector

With an 800 K difference, it seems that the reflector is extremely effective.

It was found that the Diffuse Gray change had disabled radiation loss. Enabling diffuse gray on all surfaces caused an unacceptable slowdown, so only the thin bowtie section was activated. With an "external temperature" field, got "solution trivially zero". Removed external temperature.

reflector_real

The difference between the two at 20v and 110 W is now 2518-2372 K - notably different from the previous non-diffuse-gray tests. The reflector is quite hot.

At 60 watts, peak temp was 1657 K.

With an emissivity of only 0.16, peak temperature was 1682 K. Clearly, we are in the thermal-conduction-limited regime, where the fixed mounting temperature is the dominant force. This can easily be alleviated.

The input to the bowties can either be powder, wire, liquid, or gas.

Gas will deposit on the plumbing, so power consumption will be largely the same as liquid.

#### Beam tracking

This is the fun part: feedback.

As previously discussed, the precise space charge of the beam is highly dependent on many physical factors, such as compensation by background gas, trace electrons, etc. Furthermore, each print species will behave completely differently.

Rather than design a single lens geometry capable of these features, a system that adapts in real-time to the actual beam profile may be a useful approach. This would require accurate particle position data.

- beam self-induced magnetic field

  - Fiber optic / Faraday field sensors
  - Beam optics with built-in Hall geometries
    - microvolts!

- beam space charge e-field sensing

  - ????

- Inductive or capacitive sensing

  - Quickly pulsing beam elements relative to each other may yield a measure of the gas dielectric constant. Calibration will be tricky. Pulses will have to be sufficiently fast as to avoid affecting the particle trajectories.

- Optical sensing

  - Background gas ionization / recombination light detection
  - Light transmittance / polarization /

- Beam loss feedback from lens elements

  - A small current on a lens element will indicate deposition and beam loss.

- Mechanical means

  - Faraday probes, wire scanners, witness plates, etc

- NMR?

Lens element beam loss detection should be quite simple to implement, and won't require calibration.

Beam position detectors on accelerators seem to be of the Cerenkov, silicon drift, or scintillator type, which will be ineffective for this application - see @ akiba2012charged.

@ currell1996new

@ shafer1992beam - another amazing reference

> The purpose of this paper is to review the properties of non-intercepting,
> electromagnetic beam position monitors used in particle accelerators and beamlines, and
> the types of signal processing used to recover beam position information from the
> beam-induced signals.

> There are many other possible methods of measuring beam position, both
> interceptive and non-interceptive. These include synchrotron radiation, interceptive wire
> scanners (both stepping- and flying-wire scanners), residual gas ionization and
> fluorescence, optical transition radiation, beamstrahlung, and laser probes to name a
> few. Discussion of these techniques can be found elsewhere in the literature, and in
> general review papers.

Got it to a one!

> Small loop couplers 16 (often called B-dot loops, meaning dBIdt) are simply small
> shorted antennas that couple to the azimuthal magnetic field of the passing beam and
> can be quite directional.

> After the pickup construction and assembly is complete, the electrode assembly is
> normally first "mapped" with an Rf-excited taut wire or antenna stretched through the
> pickup. The electrical response for various wire-displacement values of x and y
> determines the electrical center and the displacement sensitivities, as well as the
> nonlinearities. 13 The pickup is then installed and aligned mechanically with the other
> beamline components. An optional alternative for the final alignment is to place a taut
> wire along the magnetic axis of the beamline magnetic optics after the pickup is
> mechanically mounted, excite the wire with an rf signal, and measure the electrical
> offset (decibels of output signal unbalance) relative to the magnetic, rather than the
> mechanical, axis of the beam optics. 42 The electrical offset and the displacement
> sensitivity are then put into the computer database for correction to the beam position
> data as it is read out. The nonlinearities, as shown in Fig. 12, can be corrected in a
> look-up table at this time.
> In the taut-wire measurement, the signal on the wire is by definition a TEM
> (principal) wave with no longitudinal electric or magnetic component, which travels at
> the velocity of light and emulates highly relativistic particles. The signals associated
> with slow particles, as discussed above and illustrated in Fig. 10, are very difficult to
> generate on wires. As shown above, because the pickup response depends on the
> particle velocity, this effect must be considered in analyzing the wire measurements.

Clever! We can try different geometries and positions to build a regression.

Beam-modulated capacitive sensors seem to be ideal to get us the charged particles. How about the uncharged ones? I guess we'll deal with that later.

Select lens elements could be split into quadrants and measured differentially, even with a potential applied.

Sorry, "window-frame"? Yeah, bowtie is probably an acceptable transgression.

Modulated beam capacitive coupling - equation 6.4 @ shafer1992beam:
$$
V_c = \frac{WL}{2\pi C} \frac{I_b(t)}{v_b}
$$
(v originally stated as beta_b * speed of light).

Some approximate numbers: if the capacitance is on the order of 10 pF, the plate is 2 mm by 2 mm, the current varies by 0.001 a in 10 us, and the beam velocity is 18 Mm/s (1000 eV, corresponding to maximum focus voltage), the plate voltage will be changed by

```
0.353 v
```

!!! Perfect!

Note that no voltage is produced at steady-state. This means that no power is transfered from plates to beam. It also means that the bowtie temperature will have to be modulated. This could be accomplished via a sawtooth wave; a slow cooling and commensurate decrease in power, followed by a large pulse of current.

Distinguishing between beam-plate collision and a beam signal proper might be a bit tricky. Oh, no it won't - the collision will be steady-state, whereas the modulation will be in-phase with the beam pulsing.

If the heavy beam alternates around 0.1 milliamp in 1/100th of a second, and speeds past at 40 km/s,

```
0.0159 v
```

#### Fluid tracking

The resistance of the bowtie will change when it is filled with conductive molten metal. That might be one of the coolest statements I've ever made.

#### Amplifiers

The cheapest 600v MOSFET or IGBT on Digikey seems to be ~\$0.10 at 3000-of pricing. With the minimum 5 plates and 2048 bowties, this would cost over $1000. Clearly, the amplifiers will have to be vertically integrated.

> Nickel is used mainly because is has high resistivity which makes is easy to weld.

Ah! I had assumed that there was an electrostatic reason. Surface contamination is a significant concern, as Erdman & Zipf described (haha EZ lens!).

Since there is no "blanking" feature on the ion printer, the beam is always present; therefore, the slew rate of the plates must be quite high to prevent material from being deposited between positions.

Given a triode with a 500k anode resistance, and a plate capacitance of 300 pF, a time constant of ~200 us can be expected.

To decrease power consumption, the bowtie could serve double-duty as the amp cathode heater. The reflector shield could be coated with barium oxide paste, serving as an indirectly heated hot cathode.

Simulations will have to be performed to determine the ideal

#### Electrophoresis test 2

Graphite and 12L14 were used as the cathode with an aluminum anode. Voltages of 40 to 120v were attempted. 0.04 a were drawn. No deposited layer was observed. PVA binder was added to the mixture. No deposited layer was observed.

#### Anodization test 1

Two pure aluminum wires were inserted into a room-temperature bath containing 20g of sodium bisulfate dissolved in 100g of tap water. Stirring was maintained throughout. 40v was applied, and the electrode began drawing 0.3a. The anode effervesced profusely.  The anode was removed after ~5 minutes, when the current had dropped to 0.1a.

Lungs were found to tickle slightly. The anode had been very effectively anodized, and had taken a dull gray lustre. The coating was reasonably scratch-resistant, requiring a fine point to break the surface. The wire was hardened significantly. The resistance was above ~100 Mohm. Breakdown voltage tests were not run.

Graphite can be used as an electrode for anodizing clear.

I do not believe I will anodize again; the sulfuric acid mists created by the type-3 process are really spicy, and it was a little hard to breathe last night. My sinuses were visibly swollen. My hood is clearly insufficient to protect me.

#### Vacuum induction furnace test 1

A 1kw liquid-cooled induction heater was used to heat a piece of graphite inside an evacuated test tube. Failure.

#### High-current transformer graphite test 1

A transformer constructed of 6 ga wire, known to produce peak currents of >100A, was connected across a small graphite mold. The mold was not heated appreciably.

#### Graphite resistivity

The prototype bowtie was 0.75x0.6x10mm, and had a resistance of 0.33 R.
$$
RA/L = p
$$
Graphite therefore has a resistivity of approx. 14.9 uOhm-meters, or 67110 S/m. The value used for the Elmer sim was 3500 S/m - this explains the discrepancy.

The sim value was obtained from @ lutcov1970thermal.

Appending my notes from the .sif file:

> ! Graphite value is a rough approximation to the data provided in
> ! Lutcov, A. ., Volga, V. ., & Dymov, B. . (1970).
> ! Thermal conductivity, electric resistivity and specific heat of dense graphites.
>
> ! Specific heat data is from Thermal Properties of G-348 Graphite
> ! Donald M. McEligot, W. David Swank, David L. Cottle, Francisco I. Valentin
> ! Mr. Swank, you've got a cool name.
>
> !I've confirmed that the volume resistance values returned are sane for Aluminum.
>
> !For comparison, using
> !graphite data directly from McMaster-Carr,
> !(dividing ohms/sq by the thickness of the sheet, which is horrifically inaccurate)
> !I get 0.00001397 ohm-meters
> !or 71582 S/m.
>
> !Screw this.
> !I just put my block of graphite across my bench supply,
> !and obtained a value of 0.66 ohms,
> !1968.5 S/m.
>
> !Using my bench meter in Kelvin-probe mode, I obtained a value of
> !0.221 ohms,
> !5873.9 S/m.

The observed value matches the value from McMaster-Carr to exceptional accuracy. All other values are ridiculous. The new value has been substituted.

#### Anodization test 2

Diluted the anodize bath significantly. The rest was violently neutralized with sodium bicarbonate. Tests conducted at various voltages still yielded great anodizing power even at ~50x dilution. The anodization far more porous and pitted.

#### "Dirty" chamber

Some 3" OD x 1/8" wall lexan tubing was found.
$$

$$
#### Hot Surface Igniters

These are essentially miniature versions of the SiC heating elements used on commercial high-temperature kilns. The SiC ones are quite delicate, but there are Silicon Nitride sandwich versions which are apparently much stronger. The SiNi ones seem to have a lower peak temperature, however.

Thinking of building a real high-temp furnace with these. Kind of tired of messing about with torches etc. At ~4 A each, we can only run 4 on a standard 1800 W circuit.

Silicon Nitride decomposes at ~1850 C. The SiC elements may be more optimal for this application.

SILICON-CARBIDE/BORON-CONTAINING COATINGS FOR THE OXIDATION PROTECTION OF GRAPHITE - it seems that SiC layers on graphite tend to crack. Addition of boron can solve this issue.

MoSi elements are also available.

However, I have a lot of graphite, and I already know that graphite is easily capable of these temperatures - it's a high TRL heater here. If I make a graphite plate 70x25 mm, with 7 runs of 1.5x2.5mm cross section, I will obtain a resistance of 1.947 R, a cool 25 a at 48V.

#### FAST/SPS ceramics / Polymer Derived ceramics

Spark Plasma Sintering seems an achievable technique for production purposes.

#### Faster Laplace computation

<https://people.eecs.berkeley.edu/~demmel/cs267-1995/lecture24/lecture24.html>

> On a realistic parallel machine, one would simply assign grid point (i,j) to processors in a block fashion as shown below, and have each processor update the values of U(i,j,m+1) at the grid point it owns. This requires U values on the boundary of the blocks to be communicated to neighboring processors. When n >> p, so that each processor owns a large number n^2/p of grid points, the amount of data communicated, n/p words with each neighbor, will be relatively small.

<https://github.com/NVIDIA/AMGX> is also an option if these methods are insufficient.

> At least a grid dependency study
> must be carried out to verify whether the solution basically remains the same
> when the computational grid is refined.

[http://ftp.feq.ufu.br/Luis_Claudio/Books/E-Books/Food/Food%20process%20modelling/35652_04.pdf](http://ftp.feq.ufu.br/Luis_Claudio/Books/E-Books/Food/Food process modelling/35652_04.pdf)

@ demmel1995

@ nagel2011solving

See @ yavuzturk2005assessment 4.3, (2) for heat flux and transient thermal modelling.

dirchlet conditions

#### Beam diagnostics at scale

The cheapest comparator (required for a successive-approximation ADC) at 10000-of pricing is ~\$0.14 / 4 elements, which would cost >300 for a 2048-element printer.

A single NPN transistor is only $0.03, however, and a standard long-tailed pair only requires two transistors. We're not concerned about linearity or really any aspect of dif

A 16-channel analog switch (the CD74HC4067M96, for instance) is $0.52. If 8 channels are required per beam, this comes to \$520.

Digital muxes cost

A grid matrix AND system could be arranged, requiring only two transistors per output.

Some sort of VCO could also be designed.

#### Hybrid probe

Theoretically calculating precise energy/momentum balance and ionization percentages in electron-beam ionization appears to be almost impossible. Coefficients for heavy atoms like aluminum and iron are scarce, and the underlying theory is highly quantum mechanical. VSS/VHS parameters alone will likely be insufficient.

Accuracy of ~1 percent is important - even a small amount of misdirected material will destroy both the printed object and the assembly.

For this reason, we are going to harness the most powerful simulator ever: the universe itself.

Previously, I was going to determine the deposited mass using a combination capacitive spring balance and Kelvin cup. However, given the small mass, the capacitance change will likely be infinitesimal.

Deposition thickness measurement is usually done by determining the change in frequency or Q factor of a quartz resonator.

I experimented with using a small 3-wire feedback piezo sensor; however, these are constructed from brass and resin insulation, neither of which I would like to have present in the high heat flux immediately surrounding the bowtie. Standard quartz oscillators seem to be constructed from vacuum-safe materials.

To simplify measurement,

I was also planning on making the microbalance and Kelvin cup one and the same; however, this would require an electrode mounted to the quartz resonator, making the setup somewhat more complex.

A pair of plates perpendicular to the Kelvin cup entrance can be used to preferentially deflect electrons.

The beam calorimeter can be calibrated by dissipating a known power into an integrated SMD resistor.

The Teensy

A stepper motor and counterbalance will be used to

Effects that will have to be calibrated out:

- Radiated heat from the bowtie
- Change in emissivity as material is deposited

Purchased 5 Abracon ACO1847 1 MHz oscillators. One was sacrificed to determine the position of the internal quartz element. It appears to be less than 0.6mm from the top of the casing and 8.13 mm in diameter, with 6 mm safe distance between the mounting supports). Looking at the oscillator upright, with the text readable, the first mounting peg is 8.8 mm from the right side (measuring from the body, not the flange) and 6.58mm from the bottom.

The second mounting peg is 16.14mm from the right and 2.15mm from the bottom.

The crystal element is 0.208mm thick.

@ mueller1968direct

> This latter situation is the usual
> one, since the total loading of the crystals should be
> limited to 1% of the mass of the crystal.

Things which should be mounted to the measurement head:

- Oscillator
  - Sensing either via oscilloscope or Teensy
- Kelvin cup
  - Calibration resistor
  - Thermistor
  -
- Bowtie mosfet
-

<http://www.stabitech.nl/Quartz.htm>

#### Cascoding

HV Cascoding is a powerful technique, though it is not without idiosyncrasies. Amplifying the ~5 KV extraction supply would require 3 or 4 HV mosfets per emitter.

#### SiC furnace construction

An Emerson 767A-372 Carbide hot surface igniter and an Amaco 28035N 9" x 4-1/2" x 2-1/2" firebrick were purchased.

The firebrick was cut in twain with a wet diamond tile saw, a 27mm slice was rended from one of the halves, and a pocket was made in the remnant.

Holes for the igniter were drilled into the slice using a standard drill bit. The igniter was mounted using 1460c high-temp cement. The cement had dried considerably, and was not able to adhere to the wet-cut surface.

The assembly was left to dry for several hours.

The igniter body appeared to be made out of steatite C220, not alumina; therefore, a ~7mm firebrick gap was added to insulate the low-temperature side of the igniter. This was probably not necessary; Steatite has a maximum temp of 1700 C, likely higher than the furnace will ever attain.

Firebrick cuts very easily; mounting on the CNC may have been possible.

#### Firing

Fired up the new crucible. It performs beyond my wildest dreams. Measured the internal temperature with a small thermocouple stripped of insulation. It hit 500c at a mere ~50v (of 140), 700c at ~80v. The temp was maintained at 400c for ~30 minutes to bake off any residual moisture; some slight hissing was heard.

The outside is still cold to the touch.

120v rapidly drove the kiln past 1000c.

#### Alumina + Kaolin test 2, new furnace

A digital control system was set up to drive the new kiln; however, the only SSR available was apparently burned out.

A 70% Alumina / 30% Kaolin / 19% water solution was made. This was far too liquid.

Impatience caused the temperature to rise to ~200c far too quickly. Distressing popping noises were heard.

The kiln was brought to 1300c for ~5 minutes. This required ~130v.

The part had broken, but was composed of the most wonderful hard alumina. A few more minutes at temperature would probably be in order. Some residue was deposited onto the surface of the SiC element.

#### Furnace PID

A new SSR was purchased, and a little rubbish PID algorithm was written to control the kiln. 1,1,4 with integral bounds of -300 and 300 was effective - oscillations of +-20C, no problemo. The element draws a consistent 3.7A throughout the the temperature range.

Thermocouple melted.

Various tests were performed with different mixture viscosities.

Alumina-dipped graphite was very effective; it seemed to bond well to the surface of the graphite. The graphite degraded significantly, however; it had lost almost all structural integrity after two sintering tests.

I was planning on making a spectroscope pyrometer; however, I realized that this wouldn't give me any measurements at low temperatures - required for furnace bakeout.

Tried measuring how tungsten wire degrades in atmosphere; used a lighter to heat a 0.1mmx20mm piece red hot while measuring its resistance with the bench meter. Resistance went from 2.630r to ~3.35r when hot, but returned to 2.54 after one cycle, then 2.4 after the next, etc. Not a reliable thermistor.

Err, the above effect may have been a contact resistance problem.

Tried 100r divider with a length of nichrome in the furnace. Reading unchanged over temperature range.

Used proper kiln thermocouple from other kiln. Worked as expected - small temperature offset at maximum temperatures.

#### Delrin alumina casting

A one-sided mold was cut from 1/4" delrin, and clamped to a flat piece of delrin. A 70/30 alumina mix was made.

This was left to dry for ~30 minutes, and then opened. The alumina had not yet dried.

#### Aluminum graphite coating

An aluminum coupon was dipped into 70/30 alumina, forming a thin insulating layer. A blowtorch was used to sinter. The aluminum melted slightly.

I don't have any steel. Sucks.

The problem no longer seems to be related to the alumina sintering; with kaolin, this is easily effected.

#### Delrin alumina casting with PVA binder

Following the advice of @ chabert2008cross, a solution was made containing a small amount of PVA binder. This contained 1.5g kaolin, 3.5g alumina, and 0.2g PVA wood glue (solids percentage ~0.4-0.7). Less than 1.5g of water was added until the mixture was very stiff and clay-like. This was added to a syringe and injected with some difficulty into a delrin mold until clay was emitted from the sprues. The mold was immediately disassembled, and it was found that the clay had fully permeated through the channels in the mold.

Interesting: photolithography works on clay <https://ceramicartsnetwork.org/daily/ceramic-supplies/ceramic-colorants/photo-lithography-on-clay-a-surprisingly-simple-way-to-print-images-on-clay/>

#### Green machining

oh it's a green machine

very green

penny lane -

The previous mixture could not be released from the mold; it was too brittle, and snapped immediately. The ejector pins functioned admirably. Some shrinkage was observed.

One of the scrap pieces was taped gently to a piece of delrin on the CNC bed. This was then milled at 24krpm, 65 mm/min, and ~0.7mm stepdown. This worked admirably.

> synergistic interaction among locust bean, carrageenan, and
> xanthan gum

bahahaha

I'm missing the DHF cross-linker that was mentioned in the study.

> Thegreen components were fired at between 1350 and 1450C for 2
> h after a 30-min hold at 3501C for PVA burnout

Perhaps using mold release would have been helpful.

#### Green cookie-cutting

Another mixture was created with 1.5g kaolin, 3.5g alumina, 0.2g PVA wood glue. Sufficient water was added until a putty-like texture was attained. This was spread out on a delrin sheet, and a delrin "cookie cutter" mold was pressed onto it with great force. The mold was then removed. The part stayed cleanly attached to the delrin sheet - occasionally, some distortion would be encountered; mold release may solve that issue. This was left to dry for ~3 hours, then transferred to the kiln. The green was strong enough to be handled.

The kiln was inadvertently preheated to 100c, then brought to ~350c over the course of 5 minutes. This temperature was maintained for 20 minutes, and then the temperature spiked to 1300c.

This process was conservative for this part, however; even the highest temperature ramp rate from cold yielded no ill effects.

The part was extremely hard and strong, though it shattered when sprue was removed; crack in the green propagated.

The temperature reading of 1100 was far below the previously observed temperature of 1300-1400; this was almost certainly an offset due to the new high-thermal-mass thermocouple.

silicon carbide; it's also very pretty!

Heat stress-testing with propane torch caused the part to both crack locally, and become very weak globally.

#### More ways of measuring liquid

The bowtie plates can be vibrated to determine their contents, or - perhaps an easier method; their thermal mass can be measured!

#### Stepper motor

> \1. RATED VOLTAGE :                                  3.3 V DC
>
> 2 .COIL RESISTANCE :                                 20 Ω±10%
>
> \3. NO. OF PHASES :                                     2 PHASES
>
> \4. STEP ANGLE :                                         18°/ STEP
>
> \5. MAX. STARTING FREQUENCY :               800 PPS min. (AT 3.3 V DC)
>
> \6. MAX. SLEWING FREQUENCY :                2000 PPS min. (AT 3.3 V DC)
>
> 7.PULL IN  TORQUE :                                   1.5 gf-cm max. (AT 500 PPS  3.3 V DC)
>
> 8.PULL  OUT TORQUE :                                2.0 gf-cm min. (AT 500 PPS,  3.3 V DC)
>
> INSULATION CLASS :                                CLASS E FOR COILS
>
> INSULATION STRENGTH :                       100 V AC FOR ONE SECOND (3mA MAX)
>
> INSULATION RESISTANCE :                    1.0 MΩ (DC 100 V)  
>
> OPERATING TEMPERATURE RANGE :   -10 ~+60 ℃

Let's say mine can do 1 gf-cm.

#### SiC element bubbling

The SiC element in my kiln produced some massive bubbles! An explanation for these can be found in @raj2015.

#### 90% alumina

90% alumina for 40min at 140v works well.

#### Ceramic ingot

Merely molding ceramics into a rough shape is not sufficient; bubbles and porosity are apparent.

A large delrin die was made to press into a suitable ingot; this worked reasonably well, though there were some imperfections on the bottom of the ingot.

If the mold or press does not work, the material can be recovered; adding some clay functioned perfectly.

#### Momentum balance

We're trying to find the momentum balance of collisional ionization. The device uses a quartz microbalance, and is balanced precisely.

It's a balanced balance-balance.

#### Green machining 2

Tried machining some 90/10 alumina. First attempt was at some 1000mm/min, reasonable surface finish on some areas but fine details just cracked.

Second attempt was at 100 mm/min, same deal.

Acetone dissolves polystyrene, but not PVA. Might be an interesting mold technique.

Unfortunately, acetone also seems to dissolve the green rapidly - possibly due to water contamination in the acetone.

Ordered some nice machinable wax that's supposed to burn off cleanly; some variation of wax burnoff while drying the green may work. The tricky bit is getting within that hysteresis between part contraction and cracking, part too wet and weak to support itself stably, etc.

#### Nitinol vacuum actuator

The gear and stepper system was causing some consternation; first, the torque is extremely low, only ~1g. I was reminded of SMA muscle wire, which is often used for this exact application.

A torsion spring or counterweight is required to tension the wire.

#### Grid beam position monitor

#### Capacitance simulation

<https://physics.stackexchange.com/questions/24072/calculating-capacitance-of-arbitrary-plate-shape-and-arrangement>

> You make a grid, place your shapes on the grid, and solve Laplace's equation with a zero potential at infinity, and some potential on the grid. This will give you an electric field intensity at every point (the gradient of the potential), and you sum up the implied charge. The ratio Q/V is the capacitance.
>
> This is mathematically optimal, and the only improvement is to use non-grid approximations, like expansion in harmonics at large distances, and superior higher-order methods in the interior of the grid. For Laplace's equation on modern computers, there is no issue--- even the worst algorithm will give you an answer to 1% accuracy on an arbitrary shape within a reasonable time.

Okay, so I think I've got it.

First, we figure out the capacitance of the electrodes in the simulation. Next, for each time step, we determine the charge added to the plate via this method, compute the current through the shunt resistor and the new potential, and deposit that potential onto the plates.

The only question now is: what precisely did Ron mean by "sum up the implied charge"? Time to hit the Gauss.

#### "open boundaries"

I was planning on making the Laplace simulator ignore the edges of the boundary, rather than making them zero in the five-point star. However, this is nonsense.

Replacing the boundary condition bools with an element ID might be helpful.

#### Mesh refinement

A conservative simulation might require a 5x5x5 cm world, including regions with 0.05 mm resolution. A dumb uniform bool mesh of that size would take up almost 1Gb in memory, which is clearly unacceptable.

We don't need an adaptive mesh, but a certain level of refinement is essential.

This took a bit of head-scratching, but I think this is feasible with only a few minor changes to the mesh data structure; while reads and writes will take a few more cycles, this cost should be outweighed by the smaller number of mesh points.

Additionally, implementing a multigrid solver should be trivial.

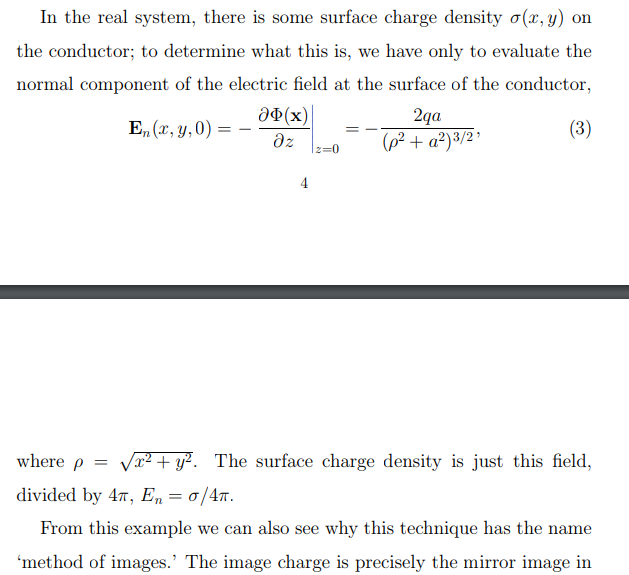
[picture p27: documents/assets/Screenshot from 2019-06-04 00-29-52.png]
Screenshot from 2019-06-04 00-29-52


Gotcha!

Thinly sliced/halbach ion optics

#### FPGA beam driver

An FPGA with 200 I/O can be had for ~$10, in case some high-speed logic is required. Per-I/O prices of FPGAs vs microcontrollers are surprisingly similar.

#### Ultrasonic bowtie excitation

Bunching of the beam for diagnostics can be facilitated by mechanical vibration of the bowtie nozzle.

#### Diffusion pump

vapor superheat post-boiling - more efficient pumpdown with lower power consumption?

Activated alumina beads for backstreaming absorption

#### Jacobi relaxation in C++

Trying to figure out the best data structure for Jacobi.

A quick Nyion test yielded 1780 ms per iteration for a single-core 200x200x200 float mesh relax, using 1d C++ vectors with a 3d lookup function. 66.9 MB of memory was consumed.

This indicates an abysmal 222.5 ns per 7-point star sum - under 5 MHz! Ouch! I know, premature optimization and all that, but this is kind of a fundamental design issue; everything centers around this.

The Jacobi function will take thousands of cycles to converge, and will be called every time charge should  be deposited onto the PiC grid; that is, every time a particle moves into another grid; so it's really quite critical.

What's our goal? The rule of thumb is that 10 space-charge points are required to accurately model a beam. The nozzle is 0.4mm in diameter, so a 0.00004m mesh is required around there. The current generation extractor is 9mm in diameter, so 225 mesh points across the x.  200x200x200 is probably a reasonable estimate.

Then, we'll need at least 1000 J or G-S cycles for convergence (with some multigrid action, surely), times 0.2 meters / 0.0001 = 2000 iterations as the space charge fills in. That's around 2 M J cycles - three weeks or so at 1.8 s each.

Some beam envelope tricks could probably pare this down to 10-20, but I don't wanna be clever.

So, is 5 Mhz all we're going to get? Assuming 100% cache misses, DDR4-1600 can hit 12800 MB/s. Divide by 4 because we're working with floats, divide by 8 for the stencil, then by 10 because this is silly best-case nonsense = 40 Mhz.

There's some room for improvement, but probably not the several orders of magnitude that are required.

For the hell of it, I swapped out the 1d C++ vectors for a simple 3d array on the global heap. This required only 100 ms / cycle!

Okay, so I guess we're still CPU limited - those ~10 index lookups were probably killer.

Time for some testing!

```
relax_laplace(){
 auto t1 = std::chrono::high_resolution_clock::now();
  potentials[1][1][1] = 10;
  for(int i = 0; i < 10; i++){
    for(int x = 1; x < mesh_geometry[X]-1; x++){
      for(int y = 1; y < mesh_geometry[Y]-1; y++){
        for(int z = 1; z < mesh_geometry[Z]-1; z++){
            potentials[x][y][z] = (potentials[x-1][y][z] +
                                                     potentials[x+1][y][z] +
                                                     potentials[x][y-1][z] +
                                                     potentials[x][y+1][z] +
                                                     potentials[x][y][z-1] +
                                                     potentials[x][y][z+1])/6.0;
        }
      }
    }
  }
  auto t2 = std::chrono::high_resolution_clock::now();
  std::cout << "each cycle took " << (std::chrono::duration_cast<std::chrono::milliseconds>(t2-t1).count())/10.0 << " milliseconds" << "\n";
  return potentials[0][0][0];
}

time_lookup(){
    t1 = std::chrono::high_resolution_clock::now();
      for(volatile int i = 0; i < 100; i++){
        volatile int test = potentials[i][i][i];
        asm(""); //prevent this loop from being optimized out
      }
      t2 = std::chrono::high_resolution_clock::now();

      std::cout << "idx took " << (std::chrono::duration_cast<std::chrono::nanoseconds>(t2-t1).count())/100 << " us" << "\n";
}

int i_idx_arg(int x, int y, int z, int x_len, int y_len, int z_len){
  return (x_len*y_len*z) + (x_len*y) + x;
}
int i_idx_geom(int x, int y, int z, int mesh_geometry[3]){
  return (mesh_geometry[X]*mesh_geometry[Y]*z) + (mesh_geometry[X]*y) + x ;
}

1d vector-style
std::vector<float> potentials((200*200*200),0);

std::vector<std::vector<std::vector<float>>> potentials(200, std::vector<std::vector<float>>(200, std::vector<float>(200)));

1d C-style
volatile float potentials[200*200*200];

1d std::array
std::array<float, (200*200*200)> potentials;

```

| 200x200x200 array, -O3 for all | CPU Time, +/-10ms |
| :--- | --- |
| 1d std::vector + i_idx_geom(); | 1700 ms |
| 3d std::vector | 440 ms |
| 3d global C-style array on heap but without BC flag | 100.4 ms |
| i_idx_geom(); | 110 ns |
| i_idx_arg(); | 60 ns |
| Single lookup with 3d C-style array (potentials\[0\]\[0\]\[0\]) | -- ns?? |
| 3d std::array [nb: defaults to stack, segfault] | 903.8 ms |
| 1d std::vector + i_idx_geom(); | 438.6 ms |
| 1d std::vector + stupid inline math (potentials[(x_len\*y_len\*z) + (x_len\*y) + x]) | 285.4 ms |
| 1d std::vector + less stupid inline math (potentials[(xy_len\*z) + (x_len\*y) + x]) | 279.3 ms |
| 1d C-style array on heap + less stupid inline math, no BC flag | 127.7 ms |
| 1d std::array + less stupid inline math | 426.0 ms |
| 1d boost::array + less stupid inline math | 293.0 ms |
| 1d std::vector to 1d C-style arrays, then back | 175.2 ms |
| 1d std::vector to 3 cache-aligned C-style arrays on heap, BCs re-added after relax cycle to skip slow flag (MPI easy, spectral radius comp easy), then back to vector | 108.4 ms! |

Note: values do not include allocation/construction/initialization time.

Juicy! This is probably of sufficient utility that I should publish it separately.

Next, we'll need a provision for storing multiple grids within multiple timesteps. I think the 1d std::vector is the best option; despite being 2 times slower, it's much more versatile.

For some reason, adding the boundary condition check makes the system 4 times slower. Curious! This doesn't happen if I check against the same potentials[] vector. Some strange cache effect?

Changing to unsigned char had no appreciable effect.

Ah, but converting std::vector to a dynamic c-style array, performing the computation, then deleting the original array is very fast.

#### Multigrid

Tried performing multigrid (that is, seeding a fine mesh with values from a coarse mesh) "in-place" in the same array, with a greater first pass step; however, this caused a number of issues.

Also, I seem to have completely forgotten about the data structure.

#### HV Safety

A mechanical pressure interlock could be used to short the HV supplies until a suitable vacuum has been reached. A mechanical flag could also prevent the chamber from being opened until the supplies are shorted.

#### Data structure 2d: electric boogaloo

A ragged 1d array of 1d arrays. The size of each sub-mesh in world-space is fixed; the resolution is determined by the size of the 1d sub-arrays. Meshes are initialized with zero size; those parts which are active have a size.

Do we need 3-level refinement? Let's see. Let's take a worst-case scenario, where the mesh is the same size as the printer chassis; 0.5x0.5x0.5m. Splitting this into 3mm cubes would take only 170 mesh points; perfectly reasonable. Each cube would then have 216 cells.

In this case, a 2d vector has a 42% overhead over simple 2d arrays. I think that's acceptable.

The following assumptions will be made:

- The root mesh need not be square, but all submeshes are. This lets us use the submesh array length to determine each submesh resolution; this will cost 1 cube root every ~216 stencils, but saves us a bunch of array lookups.
- Submeshes can have arbitrary resolution.
- Radiative transfer will only occur within meshes with equal world spacing.

On second thought, scratch all that. Having a variable submesh resolution means indexing directly into the mesh will be impossible. This wouldn't be a huge deal, except applying the laplace stencil across submesh boundaries will be difficult and slow, I think. That is, negative indices would have to be caught, the previous submesh indexed into, and the previous submesh index computed.

This is bustin' my noodle! Let's hardcode the submesh res for now.

#### Magnetohydrodynamic metal pump

Magnetic liquid-metal pumps are quite common in nuclear reactors. This would be perfect for the

<https://www.mikeash.com/pyblog/fluid-simulation-for-dummies.html>

A third alumina layer can be used between two graphite layers, with a labyrinth seal between each layer. Also solves the stiffness problem.

Mold could be made such that the graphite part is put inside and an even coating of alumina is added around all surfaces.

alumina mixed with silicone oil?

The space shuttle leading-edge RCC heatshield tiles had a similar silicon carbide conversion coating for oxidation protection.

If a liquid ring roughing pump is used, it'd be cool to have the workings visible.

Could a magnetohydrodynamic pump be used with a liquid ring? Interesting...

No, liquid-ring pumps are not likely to be effective for this purpose; the base vacuum is not sufficient for diffusion pump startup.

#### More laplace

Got mesh refinement and multigrid working, both are very effective. Convergence is still a bit slow on the ol' laplace.

Tried 9-point, SOR 1.2 to 1.7, still doesn't converge quickly.

Tried a very slow multigrid progression. This works really well for meshes with <10% BCs. Convergence on a 200x200x200 mesh to 0.01 takes about 3 minutes. 100x100x100 takes 15 seconds.

#### FPGA-accelerated laplace

3 minutes to converge is a bit much. I could parallelize this, but have to learn verilog for school, and happen to have a DE0-Nano FPGA dev board with 32 MB of sdram, which will fit a 200x200x200 array perfectly. GPUs aren't ideal for these sorts of problems.

Transferring data to the fpga at reasonable speed presents some difficulty; the built-in USB blaster can apparently hit ~10 Mbps, but the bindings that exist only allow ~10kbps. UART implementation is non-trivial because of clock domains etc. An RPI might work: socket -> wide gpio bus; direct port maniuplation in C++ can hit a few dozen Mhz. Ordered an FT232R high-speed parallel FIFO.

the "Kaczmarz method" is apparently guaranteed to converge.

I think I can convert to integer operations by multiplying by 1000 or so; this should speed everything up. A 24-bit signed int should suffice.

"Go Fish: the FPGA accelerated poisson solver"

Computer crashed a few times, needed sudo mv /var/lib/mysql/tc.log /var/lib/mysql/tc_bkp.log.

bunch of stuff happened off-camera

So the new laplace relax algorithm can do a solid 80M stencils per second, and converges in about 50 seconds to a 200x200x200 array with 6 steps of multigrid and all integer ops. There's still a possible ~3v error or so at delta 0.01 convergence; it'd be great to get that down.

> The Conjugate Gradient Method is the most prominent iterative method for solving sparse systems of linear equations.
> Unfortunately, many textbook treatments of the topic are written with neither illustrations nor intuition, and their
> victims can be found to this day babbling senselessly in the corners of dusty libraries.

CG/ method might be useful.

The "DE10-NANO CYCLONE V SE SOC KIT" by terasic has a cool 1 GB of RAM. Only dev boards with SODIMM slots seem to have larger memories.

If we halve our mesh resolution to

<hr>

```

Trials of HPC, act ii

User: "Computer! I desire a 100 TB float array."
KERNEL: [ moves to acquiesce, and falls bodily to the floor in the process ]
User: "No, no, ignore that!"
User: "Get up!"
KERNEL: [ sobs gently without moving ]

[ REAPER enters ]
[ REAPER is dressed in bobby's outfit with SCYTHE slung across arm ]

REAPER: " 'roit! What's all this about?!"

[ REAPER sees LINUX lying in a heap on the floor ]

REAPER: "ah!"
REAPER: "..."
REAPER: "ah!"
REAPER: "..."

[ REAPER begins to swing SCYTHE ineffectually and at random ]
[ REAPER knocks over flowerpot, which smashes to bits on the ground ]
[ REAPER gives KERNEL a gash across the leg ]

REAPER [ out of breath ]: "is-" [ pant ]
REAPER: "is that better?"

EarlyOOM: don't leave home without it

```

```

"Jacobi's just averaging? Let's try it out!"

Numerical methods are a gateway drug.

"Ah, what a wonderful gradient! Why, it almost looks physically correct!", you muse. "It'd be prettier in 3d, though."

Next, you're loading up objdump to eek out the that last 12% you know is lost in the implementation. You acridly reassure yourself that you're *not* the root of all evil, that Knuth would be proud. Nevertheless, you avert your screen from the gazes of those peasants around. They wouldn't understand.

You're cache-aligning, but your methods are hit-or-miss.

Soon your life is downwards everywhere. Everything relaxes but you. You stand at the street corner, watching for non-zero second derivatives. Sunlight warms your pallid skin - nothing but a radiation condition with a conductivity term. The tepid breeze sends shivers down your spine nonetheless - the convection term and its ungainly unknowns have always strained your nerves. Your most valued possession, clutched in a paper bag; an FPGA PCIe board.

Your eyes begin to blur. *this must be multigrid!*, you say.

Prof. Shewchuk's words echo vaguely within your mind. *"Of course, a procedure that always converges to zero isn’t going to help you attract friends."* If only you could find the solution.

A truck stops abruptly - too abruptly. Your eyes snap and crackle. You raise a tire-iron.

```

<hr>

It would be much better to use <https://www.mcs.anl.gov/petsc/documentation/index.html> PETSC. However, I'm really tired of dependencies right now; I grow weary of thousand-page user manuals and opaque data structures.

Trying to implement CG, which apparently converges in ~ sqrt that of gauss-seidel if properly preconditioned.

Eh, perhaps it's not worth it. A better multigrid implementation may be better use of my time.

Ah, no - there's just something wrong with the solver. Here's a single active point:

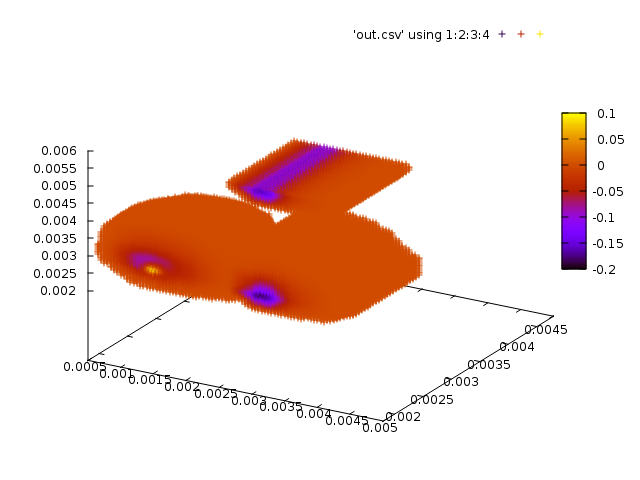
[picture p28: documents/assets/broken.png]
broken


That's not right.    

Multigrid solvers typically use a V-cycle.

For poisson, the optimal SOR coefficient is known and is around 1.96 for these problems. However, the solver becomes hopelessly unstable.

Oh, fascinating! The absolute value and units chosen greatly affect the convergence rate! <https://scicomp.stackexchange.com/questions/14809/why-should-i-renormalize-physical-variables/14810#14810>

 Switched everything to doubles, not a huge difference.

Interesting: letting coarse multigrid iterations converge too far can be detrimental

Aha! I had previously left the boundaries in the coarse residual grid; however, this was incorrect. Also, I was using a totally incorrect multigrid procedure. Here's the right one:

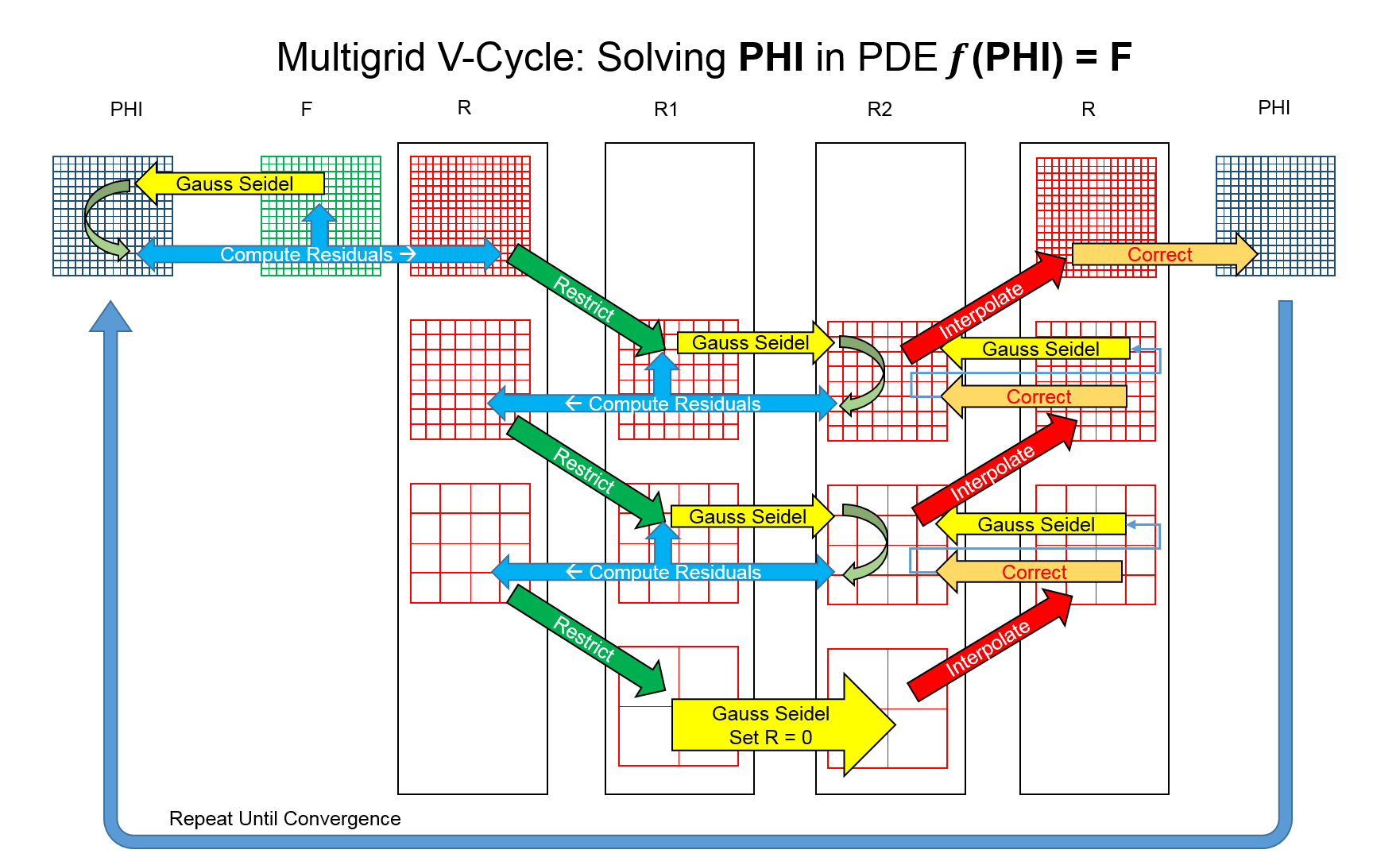
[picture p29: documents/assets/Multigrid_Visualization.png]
Multigrid_Visualization


(By ansariddle - Own work, CC BY-SA 4.0, https://commons.wikimedia.org/w/index.php?curid=52309844)

umfpack has some nasty memory limits though.

The effect of value scaling is called "condition number".

<hr>

Okay, so I've been picking at little bugs all over Nyion, and I've realized that there's something fundamentally wrong with the way I develop software. Everything seems to rapidly devolve into a blob of linear code that can only be tested through blind trial and error; TDD falls by the wayside, etc.

The same thing happened in my last major codebase.

I don't want to adopt any pseudoscientific dogmas like agile et al. I wholly abhor absolutes in engineering, as I think they lead to myriad problems ranging from overconfidence, blind rules-following without the requisite meta-analysis required for real science, etc.

MISRA C is an excellent example.

> In view of the apparent widening influence of the MISRA C standard, this paper attempts to assess whether important deficiencies in the original standard have been addressed satisfactorily. Unfortunately, they have not and the important real to false positive ratio is not much better in MISRA C 2004 than it was in MISRA C 1998 and it is unacceptably low in both.

> In its present form, the only people to benefit from the MISRA C 2004 update would appear to be tool vendors and it is to be hoped that steps will be taken both to simplify the wording and to reduce the false positive ratio in future revisions by taking a little more notice of published experimental data and being less tempted to invent rules on the basis that they seem a good idea.

> From the data obtained, we can make the following key observations. First, there are 9 out of 72 rules for which violations were observed that perform significantly better (α = 0.05) than a random predictor at locating fault-related lines. The true positive rates for these rules range from 24-100%. Second, we observed a negative correlation between MISRA rule violations and observed faults. In addition, 29 out of 72 rules had a zero true positive rate. Taken together with Adams' observation that all modifications have a non-zero probability of introducing a fault, this makes it possible that adherence to the MISRA standard as a whole would have made the software less reliable.

However, clearly something's amiss, so I'mma look into it.

<hr>

Gallium has a low vapor pressure. If gallium's propensity to attack aluminum could be prevented, it could be magnetohydro- pumped through a diffusion pump.

This is nonsense. Vane pumps are high-TRL and simple. It'll be fine.

<hr>

In keeping with the serviceability/prototyping bringup combination, it may be helpful to be able to isolate sectors of the board electronically; this would avoid having to unit test each component before assembly. For instance, each power supply could have an output switch.

<hr>

One could be forgiven for questioning why I'm rolling my own solver (and visualization, for that matter). There are many reasons: first, I want to be able to tack on new features at will (abstracting to the complex plane for EM sim, for instance).

Secondly, I'm quite tired of using third-party libraries, of dependency hell, of indecipherable error codes emerging from deep within twisted codebases, and sparse tomes of documentation. I want to know everything about the solver, how it works, under which conditions it will fail, etc.

This is nonsense, of course, but I hope it's forgivable nonsense.

<hr>
<https://en.wikipedia.org/wiki/Ultra-high-temperature_ceramics>

Whole bunch of materials like HfB2 etc developed by Manlabs that may be useful.

Zirconia is a bit  on the expensive side, also not resistant to thermal shock, but has a ridiculously high melting temp.

SiC powder is easy to obtain. Sinter temp ~1600-2000. Might work; however, still degrades on contact with aluminum. Perhaps SiC and alumina can be cofired?

Liquid silicon can be used to coat RCC.

Graphite bowtie life will probably be negligible due to aluminum carbide formation.

<hr>
Dropped LG G3 -

"Literate" coding looks pretty interesting (<https://github.com/zyedidia/Literate>)

<http://akkartik.name/post/readable-bad>

<http://akkartik.name/post/2009-01-24-19-46-26_002-soc>

<hr>

Previously, I have shirked bounds-checking on arrays for performance reasons. However, given that stencil operations are largely memory-limited, I wonder if this is still true.

Ionization electrons can be siphoned off and used

==Nyion can be used as integration test + HITL simulation software! This is big. A library should be integrated with the firmware component and used as mocks.==

Oh ho ho ho that is HUGE

We want a gradient from software to hardware, rather than a sharp, brittle distinction.

Sticker: "Hi! Thanks for buying Ionolith. I'd appreciate it if you post *any* flaws you find (down to "there's a small scratch on the back panel") on the Discourse."

Oh! rather, this can be integrated with the software telemetry. On first startup of a new machine, the user can upload a picture of any flaws.

"report a hardware flaw" command

Interesting for later use: compiling in a ramdisk can often improve performance.

<hr>

Going to switch Nyion to use only double values, negating the need for

<hr>

#### Conductive alumina-graphite nanocomposite test 1

0.06g graphite (powder obtained from block)

+0.96g Al2O3 (delta)

+0.08g white PVA glue (delta)

+0.25g water.

Putty formed normally, gray color. Sintered at 126v for 12 minutes. Temperature may have been slightly lower than normal due to gap in kiln.

Gray color disappeared after sintering; graphite was presumably oxidized to CO2, leaving behind a pure white crumbly alumina powder that was completely nonconductive.

Additionally, the 100% alumina mix appears to have failed; there was no structural integrity. This may have been due to the foreshortened sinter duration and low temp, however.

Planning on flooding the kiln with argon for the next test. This should prevent the oxidation issues, and also avoid the element degradation that was previously observed.

This burnoff property could be harnessed. A low-emissivity non-conductive shell could be made by

- Sintering fully in argon, at which point the ceramic is now impermeable to oxygen.
- Burning off the outer graphite layer in oxygen.

<hr>

However, we're still not done, because this fledgling beam does not like to exist; and as soon as it leaves the carefully controlled fields within the emitter, it does this:

Which is unhelpful. This problem is usually alleviated by increasing the beam energy, but the end user typically doesn't have the luxury of a personal nuclear reactor. The beam would also turn into a merciless death ray, slicing through the wall of the chamber and anything else in its path.

This is an issue that Feynman thought was intractable in his 1969 lecture on nanotech.

So instead, we keep the beam energy very, very low and give the beam a friend, in the form of a neutralizing electron beam. This accompanies the beam all the way to the build platform.

It is important to emphasize that I did not invent any of these concepts.

<hr>

Okay, we've got another issue: timescales. Nyion must be able to simulate bowtie transient heating, the diff. pump, the heavy beam, and the electron beam.

Heavy beam: ~30 km/s in 0.05 mm cell, 1e-9 s timescale, total runtime 1e-5 s.

E beam: 5000 km/s in 0.05mm cell, 1e-12s timescale, total runtime 1e-5 s.

Beam buttons and modulation: 20 khz, total runtime ~1e-4.

~8M mesh stencils per multigrid, 10 multigrids per cycle, ~100M cycles. Let's say we want this to run in an hour, since we'll have yet another layer for optimization.

Bowtie / thermal sim: 1e-4s timescale, runtime 10s+

Diffusion boiler: 1e-4s timescale, runtime 30s+

Diffusion DSMC: 1e-

Acceleration of Full-PIC Simulation on a CPU-FPGA Tightly Coupled Environment

<https://github.com/3cHeLoN/cupoisson/blob/master/poisson.cu>

<https://wrf.ecse.rpi.edu/Teaching/parallel-s2018/stanford/lectures/lecture_10/solving_pdes_with_cuda.pdf>

<http://users.umiacs.umd.edu/~joseph/IPDPS-2013-final.pdf>

Okay, faint glimmer of something based on 2.txt, a paper by the amazing SigFig. This is going to sound crazy, but it might just work.

What if we built an analog computer?

So the main concern with FPGAs is memory and transfer bandwidth. What if we just put together 200 boards, each with 200x200 summing op-amps?

I guess not. GPGPUs are essentially that but better.

Wait! Hol'up! We don't need to transfer the whole array each cycle, just the new particles! The (presumably static) boundaries can be pre-initialized slowly and saved.

<hr>

Uni is finished again. I have 3 weeks.

<hr>

Spent a while thinking about FPGA acceleration while studying for calc 3.

table storing cell relationships (linked-list-like)

200^3 array, about 200ms fast test.c
using openmp, g++ test.cpp -o testout -std=c++11 -fopenmp,
126 ms with 16 threads,
80 ms with 50; 30 ms with -O3.

26 ms on 64-core GCE instance with 150 threads. With -O3, 14 ms.

Where are we going to get good entropy from on an fpga?

The computational architecture required to solve this problem does not seem to exist?

I am to leave CPU Circe's company and ride the styx to the land of misinformed ideas,

<hr>

pre-compute field that would be caused by a single particle in each cell, scale by number of particles in cell, and sum

wait, that's just basically the same as using f=kQQ/r^2

That would take, say, 50x50x50 around each cell, and there are a few million

To ease routing and layout, one fpga+ram per board with fat bus interconnecting

pseudo-SRAM looks to be much easier to use, very interesting

access times for easily available DDR3 memory seem to be quite long - 15 ns write or so

This is such an interesting problem. Every time you look at it, it looks slightly different - it's limited in almost every possible way, yet still embarrassingly parallel.

hang on one goddamn minute. Where the hell did I get 2 GB from? We need 8M points, 4 bytes each, plus a boundary array. That's 64 MB, tops. The DE0-nano that I have is indeed cutting it short, with only 32 MB. A DE10

 <https://developer.nvidia.com/amgx> - only professes a 10x speedup though.

PSRAM is ~$0.2/MBit, with 50 Mhz access times.

SRAM is ~$1/MBit, with 100 Mhz access times.

<hr>

PSRAM latencies are advertised at ~70ns. However, many mobile PSRAMs feature a "burst" mode for sequential reads or writes, allowing ~10ns access.

<hr>

There's a technique called SLPIC that claims to maintain accuracy despite artificially slowing fast particles. I am wary of it.

Also, my mesh refinement routine is total garbage.

<hr>
*Nyion Accelerator*

It would be desirable for all who own an ionolith to have the capability to carry out these simulations and improve the design. Using a dedicated piece of hardware countermands this to some degree, and will introduce tremendous complexity at a critical time.

On the other hand, I do not believe that companies have time to *not* innovate. This shortsighted bias towards results is, I think, the downfall of many. Though reasonably specialized, this device would still be of some utility to the larger ion community.

Let us first attempt to reject the justification for constructing the device, and convince ourselves that it is not worth pursuing.

Assume a best-case beam runtime of 1e-5 s, a beamline distance of 0.3m, a best-case cell of 0.1mm, and an SLPIC electron slowdown on the order of 200x. Heavy beam velocity is 30 km/s; electron, 5000 km/s.

dt=4e-9 (with slowed e-), 2500 cycles.

Without slowed e-, dt=2e-11; 500k cycles. At 10 ms / cycle, this will require on the order of an hour on a Ryzen.

There is no longer a convincing argument for the necessity of FPGAs. Figures oft disappoint.

For naught but amusement, shall we compute the estimated speedup?

Assume a \$300 budget. Assume 32-bit words, 8M x16b PSRAM packages (\$7). Assume a mesh of 8M 4-byte points, x2 for multigrid, x2 for convenience + 1M particles of 32 bytes each.

This makes 160 MBytes. Now assume 2x replication for bus width.

<hr>

Let's do this differently.

There are 6 read ops and 1 write op per stencil. 8 memory modules per card would be quite ideal, then. In terms of I/O, 16 for addressing + 32 for data - almost 200 pins. That necessitates a $35 Cyclone-class or equivalent. Damn.

How about 2 modules per card? Still 80 I/O. ~50 I/O seems to be the crossover between hobbyist-class 3.3v arrays and pro 1.2v devices.

One module? 64 I/O. \$10 FPGA + \$10 in RAM. *16.

<hr>
Conrad Sanderson and Ryan Curtin.
*Armadillo: a template-based C++ library for linear algebra*.
Journal of Open Source Software, Vol. 1, pp. 26, 2016.

Conrad Sanderson and Ryan Curtin.
*Practical Sparse Matrices in C++ with Hybrid Storage and Template-Based Expression Optimisation*.
Mathematical and Computational Applications, Vol. 24, No. 3, 2019.

<hr>
<http://on-demand.gputechconf.com/gtc/2015/video/S5398.html> is a very valuable resource indeed.

<hr>

Toying with the idea of using the slow micros on each emitter tile as a massively multicore machine - probably not a good idea.

<hr>

I can hear you screaming at this document, begging me to use PETSc or some other pre-existing solution rather than rolling my own. I very probably will end up using such a library, and am ultimately being very dumb wasting time on this. However, I need a bunch of special features like complex numbers and dielectrics, and I think this'll be hard to handle with existing techniques.

<hr>

200^3 array, 100 iterations.

```C++
    for(int coord=1; coord < SIZE*SIZE*SIZE-1; coord++){
        potentials_out[coord] = (potentials[coord+1] +
                                 potentials[coord-1])/6.0;
    }
```

32 ms on one core.

```c++
for(int coord=1; coord < SIZE*SIZE*SIZE-1; coord++){
    potentials_out[coord] = potentials[coord];
}
```
2.8ms.

Adding /6: 4.6ms.

<https://stackoverflow.com/questions/25179738/measuring-memory-bandwidth-from-the-dot-product-of-two-arrays>

<hr>

```
        potentials[coord] = potentials[coord]/6;

```

-O0, single core: 58 ms.

-O0, 100 threads: 7.2 ms.

-O3, single core: 3.6 ms.

-O3, 100 threads: 2.5 ms.

```c++
    for(int coord=SIZE*SIZE; coord < SIZE*SIZE*SIZE-(SIZE*SIZE); coord++){
    potentials[coord] = (potentials[coord+1] +
             potentials[coord-1] +
             potentials[coord+SIZE] +
             potentials[coord-SIZE] +
             potentials[coord+(SIZE*SIZE)] +
             potentials[coord-(SIZE*SIZE)])/6.0;
    }
```

-O3, 1 core, 63 ms.

-O3, 30 threads, 6 ms.

As always, I have entirely misjudged the problem LIKE A DUM DUM. We're not encountering memory bandwidth bottlenecks, cache latencies, etc. IT'S JUST MY BAD CODE.

okay, fine. Let's re-write everything, toss out this stupid two-level mesh refinement thing, and get some real performance here. I think a major advantage may come from the use of ghost points rather than guard clauses on the edges.

<https://www.agner.org/optimize/#instructionset>

On the ceramics side, I should try out tapecasting.

The screen-printing system used to tapecast cofired PCBs is quite intense; a UV crosslinker might be helpful. To this end, purchased some sodium benzoate from some herbal store in TO; apparently it's an effective uv sensitizer for PVA.

sodium trimetaphosphate

Ultraviolet‐induced crosslinking of poly(vinyl alcohol) in the presence of sensitizers

Boron carbide might be another thing to try. Melts at 2700c.

Noope, seems to react with aluminum and is fiendishly brittle.

SiALON: "and exceptional resistance to wetting or corrosion by molten non-ferrous metals, compared to other refractory materials such as, for example, alumina" - melts at 1200c though.

After cofiring, it would be useful to determine dielectric constant.

```
lstopo-no-graphics
```

<hr>

For a number of reasons, the allowable timeline just became a bit shorter.

250^3 - 4 ms (9 on Ryzen)

400^3, 150 threads - 14ms (48 on Ryzen).

<hr>

Set up OpenCL with a basic stencil kernel to test some stuff.  <http://simpleopencl.blogspot.com/2013/06/tutorial-simple-start-with-opencl-and-c.html>

Just hit 2733750000 stencils per second (3 cycles).

Unreal.

I'm really, really happy.

Two showerthoughts:

1. distant blocks that don't contain particles needn't be recomputed every cycle. This should massively accelerate the startup heat-transfer phase.
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

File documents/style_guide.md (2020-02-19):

As Feynman said, it's more important to be clear rather than precise:

> **The real problem in speech is not precise language. The problem is clear language.** The desire is to have the idea clearly communicated to the other person. It is only necessary to be precise when there is some doubt as to the meaning of a phrase, and then the precision should be put in the place where the doubt exists. **It is really quite impossible to say anything with absolute precision, unless that thing is so abstracted from the real world as to not represent any real thing.**

I find that I often drift into obtuse and jargon-filled terminology, which greatly hinders understanding. Acronyms are to be abhored. 

If a technique or technology (or even variable!) is named properly, one often finds that the name alone gives you some intuitive understanding of what it means, and how it operates. "Jacobi solver" is less descriptive than Jacobi Relaxation. "Standard Deviation Of The Mean". 

All variables in all equations should be labeled immediately below. 

Any magic constants or empirical fits should have units attached.

Everything in this project should be converted to SI + eV units, unless that'd be weird (like O-ring standards)

Please don't speculate. 

When faced with a bottleneck of information about their interests, certain online communities have devolved into an unfounded, unscientific sort of speculation that I don't think is particularly healthy. The engineering world moves quickly, and there are often countless internal analyses that observers are not privy to. If you have a hunch or a theory, try to contradict it.

I will try to release information on 

sources like:

[^description]: [Internal]() [External]() 

Still not sure whether first- or third-person 

Keep it whimsical. 

<hr>

Here's something interesting.

Plugging Feynman's caltech address into the 'Hemingway Editor' yields grade 7 prose. Some snippets from FLP Vol. III: Grade 5 to 8. experiments.md: grade 12.

Griffiths QM is between 10 and 14.

<hr>

Does the practice of naming techniques after their inventors hinder understanding? 

It is important to give credit where it's due, of course, but consider this: if a paper says "Successive Over-Relaxation", you can already get an intuitive feel for what that might entail. 

"Successive": "whatever it is, we're doing it a bunch of times."
"Relaxation": "it'll start off crazy, then get to the point."
"Over": "sounds like there'd be a multiplication term in there. We're doing something 'too much' - maybe overshooting?"

SOR actually means "standard relaxation times 1.7 or so." - so we've really inferred a very accurate understanding just from the name. It's still not perfect terminology, but it's pretty good.

On the other hand, a very similar concept is known as the "Gauss-Seidel method". If you haven't experience in the field, you have to dump your cache, go hit a lookup table like Wikipedia, and try to parse its explanation. Gauss-Seidel is a general technique for linear equations, but in numerical practice it actually means "average the neighbors and update the value in-place", and this is the notion to which the authors most often refer. 'the single-matrix method' could equally be used. Of course, experts are not hindered by this subterfuge, but it might help the neophyte. 

On the other hand, maybe an approximate understanding isn't good enough. Maybe it's useful to force people to read deeply about a new technique. I don't know.

Just something to think about in case we have to name something.

<hr>

<hr>

Programming Style Guide

The command line to compile and run a program and all the environment variables should be in a comment block at the beginning. 

There's a neat documentation paradigm where example code is next to plaintext documentation. That might be useful.

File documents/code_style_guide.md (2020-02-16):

Assert (or throw exception, perhaps?) inputs to functions.

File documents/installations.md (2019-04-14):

MathGL:

Download source.

-fPIC error when cmaking with -D=enable-fltk=on

Added 

```
add_compile_options(-fPIC)
set(CMAKE_POSITION_INDEPENDENT_CODE ON)

set(CMAKE_C_FLAGS "${CMAKE_C_FLAGS} -fpic")
set(CMAKE_CXX_FLAGS "${CMAKE_CXX_FLAGS} -fpic")
```

to CMakelists.txt

Recompiled and reinstalled FLTK with 

```
./configure --enable-shared CFLAGS=-fPIC CXXFLAGS=-fPIC
```

Then built mathgl normally.

Refbase:

Installed php, php extensions, bib extensions , moved everything to /var/www/html/

`mysql_connect has been removed from php 7. Installed php5.6.`

had to reset sql password with 

```update user set plugin='mysql_native_password' where User='root';```

also needed

`sudo sed -i 's/TYPE=/ENGINE=/g' install.sql`

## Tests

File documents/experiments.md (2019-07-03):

### Dan's Fast Thin Beam Approximation

#### Background: 

Designing the focus and recombination lens poses no small challenge. High beam rigidity and charge density make conventional extractor systems difficult to implement. The radial velocity kick requirements 

Manual extractor design proved to be too slow, even with highly optimized GUI workflows and automated diagnostics.

Closed-form solutions do not exist for many possible extractor systems.

This problem is an ideal application for evolutionary design via genetic algorithms. Unfortunately, the computational intensity of standard PiC beam simulators like Warp and IBSimu make these techniques ineffective - a minimal mesh required over 3 seconds to converge on 16 cores.

After nearly a year was spent attempting to design th

Aim:

<hr>

I attempted to use a ring approximation method to simulate beam space charge. However, the program complexity quickly grew out of hand, and this concept proved unworkable. 

On a whim, I tried using a simple analytic space charge function for the beam profile. This worked very well, providing a good fit to IBSimu solutions in a fraction of the time. 

Warp was used to determining the electrode field; however, this was slow and 	 

#### Rationale

I'm mad at open-source Computer Aided Engineering.

(note: I'm not actually mad at open-source computer aided engineering. Everyone in this field is doing amazing things that I couldn't replicate in several lifetimes. This is actually just a projection of my own abject incompetence.)

Over the last 6 or so months, I've had cause to try *every single* open-source PIC simulation program, along with a few dozen computer-aided engineering and finite-element programs. I have 19.8 GB of simulation software on my disk, plus another 80 GB in CAELinux installations. 

Each PIC program generally took the better part of a day to install - usually due OpenMPI version conflicts, dependency rabbit-holes, and myriad other yak shaving.

This is a prime use for docker, you say! 

Great! Now I have to figure out how to make a virtual volume where the program wants it, enable parallelization, wait interminable times while the container is built - oh, docker just filled my drive with old cached builds.

No.

Let's examine a simple, straightforward joule heating / radiation simulation in Elmer (a great program).

1. Export .step from FreeCAD (simple, already in my workflow.)
2. Spin up VirtualBox VM with CAELinux.
3. Import .step into gmsh. (works for some parts, crashes immediately for some reason?)
4. Figure out why gmsh is crashing.
5. Run a custom bash script that creates all the 
6. Install a new version 
7. Why isn't the sim converging?
8. Refine mesh, repeat steps 3 onwards
9. Export - oh, no, exporting isn't working
10. Export to paraview.

Nevermind trying to add some esoteric feature.

In software development, a 10-second compile time (or, in TDD, test runner length) is generally regarded as unacceptable. Most toolchains are installed in a few minutes at most.

In hardware, rapid prototyping has become mainstream; the ability to conduct extremely rapid iteration is highly sought after. Most small parts can be made in under a few hours.

In firmware, I can compile, upload a binary to a microcontroller, and begin JTAG debugging the output in ~3 seconds.

The situation is such that building a physical prototype and testing it in a vacuum chamber is far, far faster than a single iteration of a simulation. 

This is ridiculous!

Moreover, this isn't a computing limitation - most simulations only required a few seconds to solve.

What if I want a diagnostic that doesn't already exist?

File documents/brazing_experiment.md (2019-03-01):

<video src="../../media/20190220_180956.mp4"></video>

<video src="../../media/20190220_182240.mp4"></video>

<video src="../../media/20190220_193405.mp4"></video>

<video src="../../media/20190220_213456.mp4"></video>

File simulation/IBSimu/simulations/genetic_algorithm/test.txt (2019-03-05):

testtesttesttesttesttesttesttesttesttesttesttesttesttesttesttesttesttesttesttesttesttesttesttesttesttesttesttesttesttesttesttesttesttesttesttesttesttesttesttesttesttesttesttesttesttesttesttesttesttesttesttesttesttesttesttesttesttesttesttesttesttesttesttesttesttesttesttesttesttesttesttesttesttesttesttesttesttesttesttesttesttesttesttesttesttesttesttesttesttesttesttesttesttesttesttesttesttesttesttesttesttesttesttesttesttesttesttesttesttesttesttesttesttesttesttesttesttesttesttesttesttesttesttesttesttesttesttesttesttesttesttesttesttesttesttesttesttesttesttesttesttesttesttesttesttesttesttesttesttesttesttesttesttesttesttesttesttesttesttesttesttesttesttesttesttesttesttesttesttesttesttesttesttesttesttesttesttesttesttesttesttesttesttesttesttesttesttesttesttesttesttesttesttesttesttesttesttesttesttest00
00
00
00
00
00
00
00
00
00
00
00
00
00
5e-050
00
00
00
00
00
00
00
00
00
00
5e-050
00
00
00
00
5e-050
00
00
00
00
00
5e-050
00
00
00
5e-050
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

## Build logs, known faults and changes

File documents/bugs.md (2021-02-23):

Going to try to emulate NASA's software methodology and note the root cause of any especially tedious bugs that I encounter. This may help improve codebase quality, or it may end up being a waste of time.

GitHub's issues page may be better suited to these reports.

<hr>

#### Issue:

Vector passed by value causes huge mesh copy at every call of a function:

```c++
relative_mesh_value(std::vector<std::vector<T>> input_mesh);
relative_mesh_value(mesh);//~10 us 

relative_mesh_value(std::vector<std::vector<T>>& input_mesh);
relative_mesh_value(mesh);//~0.11 us 
```

##### Discovery

relative_mesh_value() seemed to run exceptionally slowly. Expensive cube root calls were initially blamed, but the problem persisted even when all the contents of relative_mesh_value were removed.

##### Solution

Most other functions had the proper dereference in place. This problem could be solved procedurally by incorporating timing metrics into unit tests.

<hr>

#### Issue:

submesh_side_length returned incorrectly rounded results for certain specific values.

##### Discovery

Mesh decoarsen call failed for certain lengths. This was traced to a failure in submesh_side_length.

##### Solution

Exhaustive test procedures should be implemented wherever possible.

<Hr>

#### Issue:

```c++
int argc;
char *argv[0];
glutInit(&argc, argv); //segfaults
```

```c++
int argc = 0;
char *argv[1];
glutInit(&argc, argv);
```

##### Discovery

Commenting out an unrelated bit of code triggered this error.

##### Solution

Memory fuzzer testing would probably have caught this earlier.

<hr>

#### Issue:

Trying to switch OpenGL mode between Perspective to Ortho expended several hours of testing. It seemed that the mode change ruined the perspective rotation somehow.

##### Discovery

Removing all functions and writing a minimal test case in a separate inline loop clearly demonstrated that the 3d renderer was fine; rather, the viewpoint code was broken.

##### Solution

Particularly persistent bugs should be isolated from the codebase for closer examination if possible.

<hr>

#### Issue:

Return value neglected for custom min and max functions:

```c++
float mesh_max(std::vector<std::vector<T>> &input_mesh, root_mesh_geometry mesh_geometry){
  float max = 1e-30;
  for(int root = 0; root < mesh_geometry.root_size; root++){
      ...
  }
  ...nothing, you idiot!
}
```

##### Discovery

These functions always returned zero, which made draw_mesh very uncomfortable indeed.

Surprisingly, g++ did not take issue with this code, despite the use of `-Wall -Wextra -pedantic -Werror`.

##### Solution

All compiler warnings were disabled; they were promptly re-enabled.

<hr>

#### Issue:

Relative mesh indexing functions handle root boundaries incorrectly.

This bug somehow survived some ten rewrites of the relevant function.

##### Discovery

Convergence was very slow, even with multigrid methods.

The issue was obvious once the 3D opengl viewer was functional.

##### Solution

Ensure that unit tests also test for physical correctness. Ensure also that the success state can only be attained in the correct way; that no other combination of errors can lead to the asserted result.

For instance, if all values in an array are set to 1, any malformed array index will yield 1. Instead, all values should be initialized to zero, and only the requested point should be set.

<hr>

#### Issue:

Math within macro call subtly broken by order-of-operations

```
#define idx(x,y,z,x_len,y_len) ((x_len*y_len*z) + (x_len*y) + x)
idx(r_x,r_y,r_z+1,root_x_len,root_y_len) //13
idx(r_x,r_y,r_z+1,root_x_len,root_y_len) //14
r_z + 1 //22
idx(r_x,r_y,,root_x_len,root_y_len) 
```

##### Discovery

Rewritten relative mesh indexing function broke for edge cases. Issue only discovered due to extra time spent on unit test function; must be more disciplined in the future. 

Sprinkling printfs made the issue apparent.

##### Solution

Convert from macro to inline function to avoid such issues in the future. 

-E would be a useful troubleshooting feature, but it's breaking cmake.

<hr>

#### Issue:

Nearly a month of testing still did not yield a functional multigrid implementation.

#### Solution

Writing a proof-of-concept recipe in Python without regard to optimization very rapidly exposed the problem. This is definitely something to keep in mind; it's much easier to troubleshoot something if you know precisely the expected behavior. 

<hr>

#### Issue:

 A constant defined as double fully halved a kernel's performance.

```
(6.0*U[idx(x,y,z,X_SIZE,Y_SIZE)]
5000 us
```

```
(6.0f*U[idx(x,y,z,X_SIZE,Y_SIZE)]
2200us
```

<hr>

#### Issue:

Unit testing may be a hindrance in the early rapid prototyping stages of a project. 

##### Discovery

Many hundreds of hours were spent developing the first (very dumb) data structure; hundreds of lines of unit tests were written and thrown out as the API changed almost hourly. Eventually it became apparent that this structure wouldn't work. The new linear-stack adaptive block-structured tree shares none of the tests.

#### Issue:

Sneaky uninitialized buffers can lead to undefined behavior:

```
void sync_ghosts(){

...

    int buffer_ref_queue[MAX_DEPTH]; //store previous block reference
    int buffer_x_queue[MAX_DEPTH];  //store value index in block 
```

is broken. 

```

void sync_ghosts(){

    int buffer_ref_queue[MAX_DEPTH] = {0}; //store previous block reference
    int buffer_x_queue[MAX_DEPTH] = {0};  //store value index in block 
```

works.

#### Solution

A fuzzer would be helpful. Static analysis, too.

New instrumentation features in GCC: -fsanitize=address,undefined,null. 

#### Issue:

Very similar to the above:

```

int mesh_sizes[MAX_DEPTH] = {8};
```

actually produces {8,0,0}. 

This is perhaps the first bug in this project that was immediately caught by a unit test.

##### Solution

Making all fills explicit with 

```
std::fill(mesh_sizes, mesh_sizes + MAX_DEPTH, 8);
```

is a good idea.

Overriding the default constructor to add an initialization step might be a good idea!

#### Issue:

Adding CUDA to cmake caused a range of strange errors; the GPU reported an out of memory condition for any alloc or kernel launch and all gpu versioning and identifiers were garbage. It seemed that nvcc wasn't running the code on the GPU, but this turns out to be a known issue with Address Sanitizers:

https://github.com/google/sanitizers/issues/629

##### Solution

Not sure of a systemic way to prevent this.

#### Issue:

ASAN is not particularly reliable with CUDA code, and so I became conditioned to blaming errors on ASAN itself.

However, after spending a while trying to diagnose why ASAN was crashing even with -recover, I disabled ASAN altogether, and...

Segmentation fault.

#### Issue:

Pointer math is complicated.

Guidelines:

Choose a->b or (*a).b and stick with it. I prefer (*a).b.

Choose a sensible 'root' value to pass around. For instance, if most of your functions need a \*\*, switch to p \* = rather than p.

You can be verbose; specifically, 'return to base' constantly. If your function takes a \*\* and you want a \*, try writing:

&(**x)

Rather than 

(*x). 

Then everything feels like an atomic operation on a base. 

Perhaps there's some performance cost, but if you're working with pointers it's certainly irrelevant anyhow.

I like it! You might not, though, and that's fine.

#### Issue:

Exporting a few opaque values alieviates issues with ASAN. 

However, if the terminal crashes, I inevitably forget to export the options; and the failure modes are always so subtle.

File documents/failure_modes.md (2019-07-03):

Any observed failure modes should be put here.

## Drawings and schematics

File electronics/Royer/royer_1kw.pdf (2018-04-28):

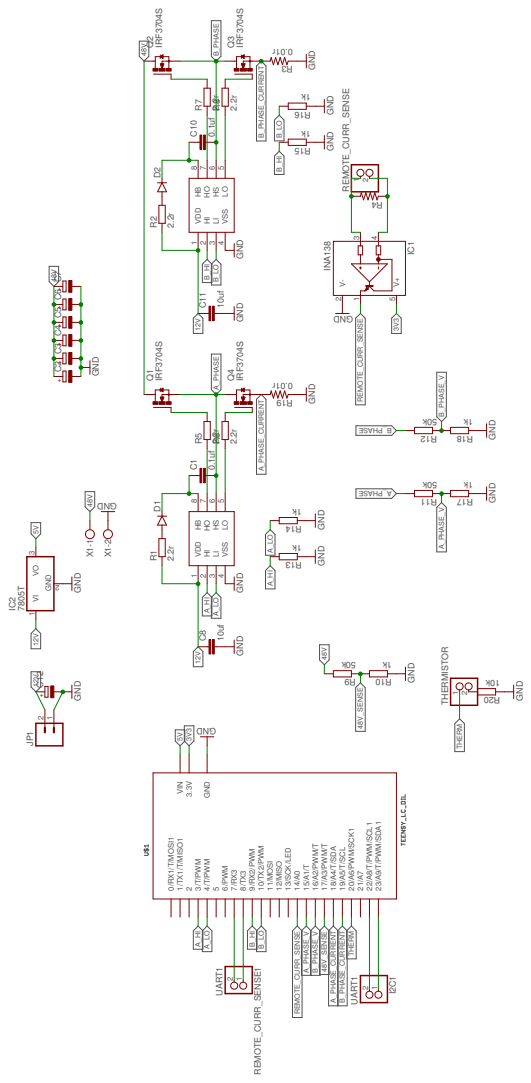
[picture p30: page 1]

DNG 2.2r 0.1uf GND GND GND GND DNG 2.2r 0.1uf GND GND GND INA138 10uf 10uf 2.2r 2.2r 2.2r 2.2r k05 k1 IRF3704S IRF3704S IRF3704S IRF3704S k1 GND k1 GND k1 GND k1 GND r 10. 0 r 10. 0 GND GND GND GND k05 k05 k1k1 DNG k01 GND 7805TGND UART1 UART1 12/MISO 11/MOSI 10/TX2/PWM 9/RX2/PWM 8/TX3 7/RX3 6/PWM 45/T/PWM 3/T/PWM 12/TX1/T/MISO1 0/RX1/T/MOSI1 GND 3.3V 23/A9/T/PWM/SDA1 22/A8/T/PWM/SCL1 21/A7 20/A6/PWM/SCK1 19/A5/T/SCL 18/A4/T/SDA 17/A3/PWM/T 16/A2/PWM/T 15/A1/T 14/A0 13/SCK/LED VIN X1-1 X1-2 VDD 1 HI 2 LI 3 VSS 4 LO 5 HS 6 HO 7 HB 8 D1 R1 C1 JP1 21 C2 C3 C4 C5 C6 C7 VDD 1 HI 2 LI 3 VSS 4 LO 5 HS 6 HO 7 HB 8 D2 R2 C10 IC1 34 1 V+ 5 V- 2 C8 C11 4 R R5 R6 R7 R8 9 R 01 R Q4 Q1 Q2 Q3 31 R 41 R51 R 61 R 91 R3 R 11 R 21 R 71 R 81 R REMOTE_CURR_SENSE 12 THERMISTOR 1202 R C12 IC2 GND VI 1 2 VO 3 REMOTE_CURR_SENSE1 21 I2C1 21 48V 48V 48V 48V A_PHASE ESAHP_A 12V 12V 12V 12V A_HI A_HI A_HI A_LO A_LO A_LO B_PHASE ESAHP_B A_PHASE_CURRENT A_PHASE_CURRENT 48V_SENSE 48V_SENSE A_PHASE_V A_PHASE_V B_HI B_HI B_HI B_LO B_LO B_LO B_PHASE_V B_PHASE_V B_PHASE_CURRENT B_PHASE_CURRENT 3V3 3V3 REMOTE_CURR_SENSE REMOTE_CURR_SENSE THERM THERM 5V 5V ++++++ +

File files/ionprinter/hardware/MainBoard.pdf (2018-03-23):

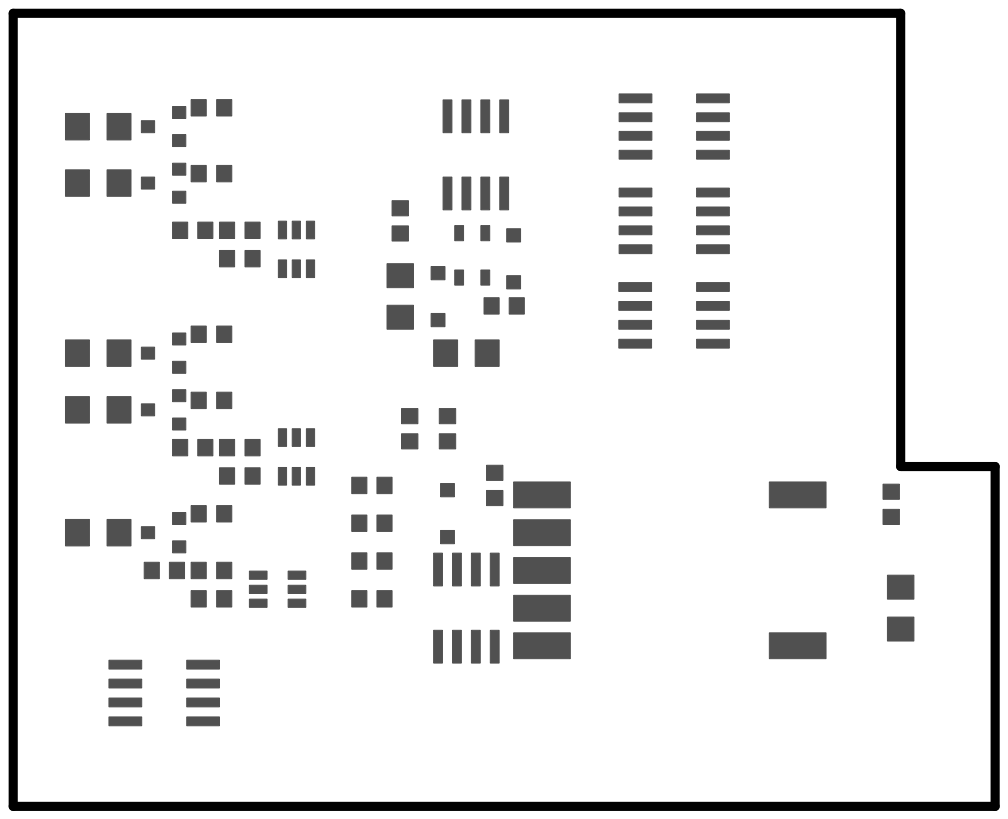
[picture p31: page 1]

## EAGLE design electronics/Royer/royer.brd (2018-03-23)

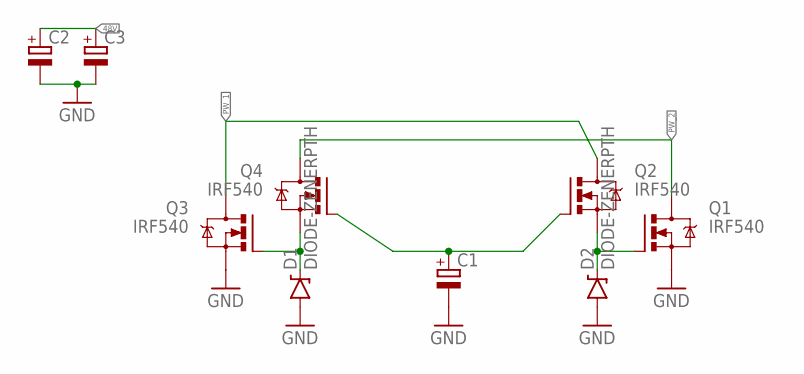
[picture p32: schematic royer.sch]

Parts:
C1: CPOL-EUSANYO_C; SANYO-OSCON_C
C2, C3: CPOL-EUSANYO_9F; SANYO-OSCON_9F
D1, D2: DIODE-ZENERPTH; DIODE-ZENER
Q1, Q2, Q3, Q4: IRF540; TO220BV

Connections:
15V: C1.+, Q2.G, Q4.G
48V: C2.+, C3.+
GND: C1.-, C2.-, C3.-, D1.P$2 (A), D2.P$2 (A), Q1.S, Q3.S
unnamed: D1.P$1 (C), Q3.G, Q4.S
unnamed: D2.P$1 (C), Q1.G, Q2.S
PW_1: Q2.D, Q3.D
PW_2: Q1.D, Q4.D

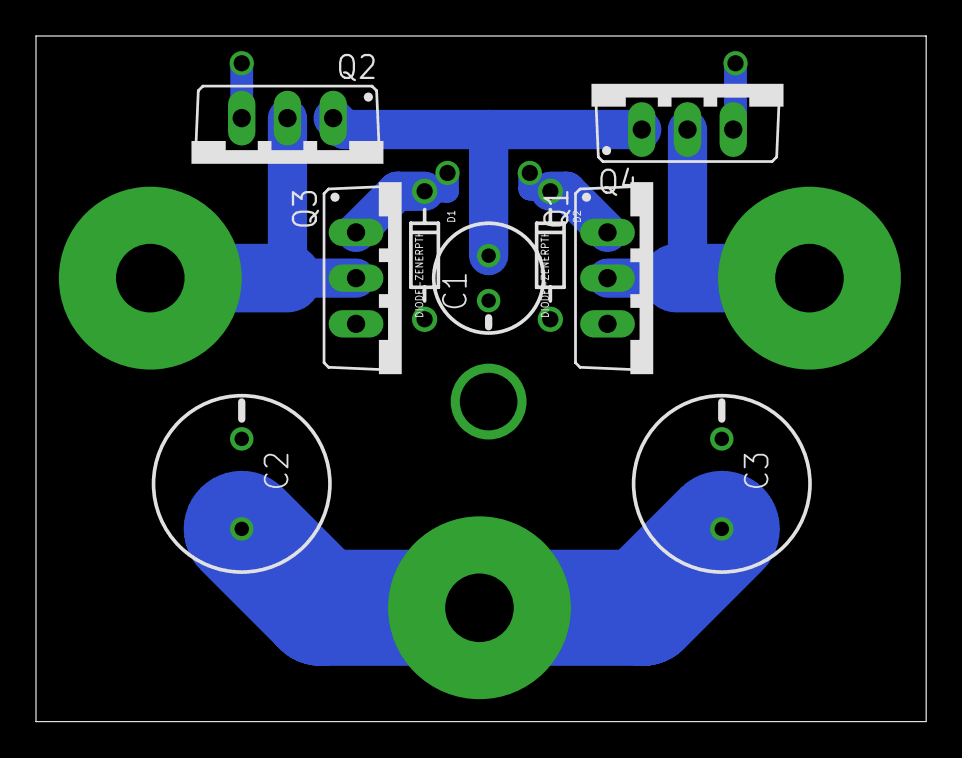
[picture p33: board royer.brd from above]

Board: 2 copper layers, 49.5 x 38.1 mm, 9 parts (0 on the bottom side), 7 nets.

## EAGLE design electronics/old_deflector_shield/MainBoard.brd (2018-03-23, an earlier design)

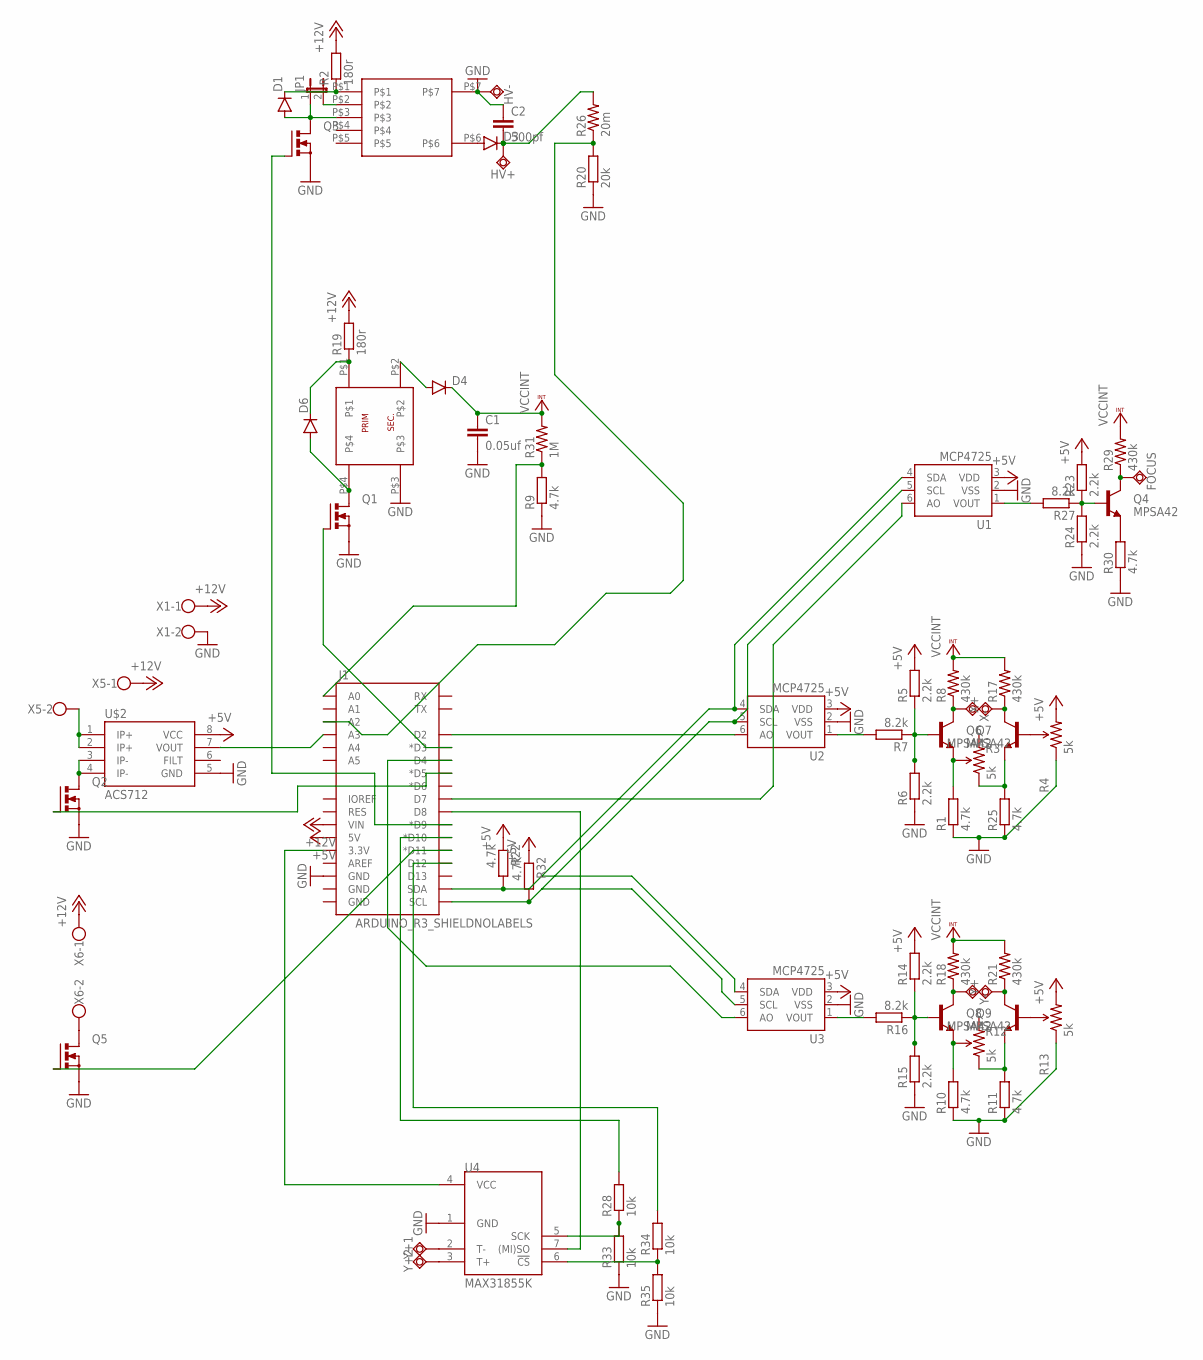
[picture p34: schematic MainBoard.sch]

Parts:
C1: 0.05uf; C1206
C2: 500pf; C1206
D1, D4, D6: DIODESOD123; SOD-123
D3: DIODEPTH; DIODE-1N4001
FOCUS: FOCUS; P1-13
HV+: TPSQPAD1-13; P1-13
HV-: TPSQPAD1-13; P1-13
J1: ARDUINO_R3_SHIELDNOLABELS; UNO_R3_SHIELD_NOLABELS
JP1: JUMPER-2SMD-NO; SJ_2S-NO
Q1, Q2, Q3, Q5: N-MOSFET-SO8S; SO-08
Q4, Q6, Q7, Q8, Q9: MPSA42; SOT23-3
R1, R9, R10, R11, R22, R25, R30, R32: 4.7k; R0603
R2, R19: 180r; R0603
R3, R4, R12, R13: 5k; TRIMPOT_PTH_S3_LOCK
R5, R6, R14, R15, R23, R24: 2.2k; R0603
R7, R16, R27: 8.2k; R0603
R8, R17, R18, R21, R29: 430k; 1206
R20: 20k; R0603
R26: 20m; AXIAL-0.4
R28, R33, R34, R35: 10k; R0603
R31: 1M; 1206
U1, U2, U3: MCP4725; SOT23-6
U4: MAX31855K; SOIC8
U$1: ATB; ATB3225
U$2: ACS712; SO08
U$3: CTX
X1, X5, X6: W237-102
X+: TPSQPAD1-13; P1-13
X-: TPSQPAD1-13; P1-13
Y+, Y+1, Y+2: TPSQPAD1-13; P1-13
Y-: TPSQPAD1-13; P1-13

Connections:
+5V: J1.5V, R4.3 (CW), R5.2, R13.3 (CW), R14.2, R22.1, R23.2, R32.1, U1.3 (VDD), U2.3 (VDD), U3.3 (VDD), U$2.8 (VCC)
+12V: J1.VIN, R2.2, R19.2, X1.1, X5.1, X6.1
GND: C1.2, C2.1, HV-.TP, J1.GND@2 (GND), Q1.1 (S), Q1.2 (S), Q1.3 (S), Q2.1 (S), Q2.2 (S), Q2.3 (S), Q3.1 (S), Q3.2 (S), Q3.3 (S), Q5.1 (S), Q5.2 (S), Q5.3 (S), R1.1, R4.1 (CCW), R6.1, R9.1, R10.1, R11.1, R13.1 (CCW), R15.1, R20.1, R24.1, R25.1, R30.1, R33.1, R35.1, U1.2 (VSS), U2.2 (VSS), U3.2 (VSS), U4.1 (GND), U$1.P$3, U$2.5 (GND), U$3.P$7, X1.2
unnamed: Q6.3 (C), R8.1, X-.TP
unnamed: Q7.3 (C), R17.1, X+.TP
unnamed: R7.2, U2.1 (VOUT)
unnamed: Q6.2 (E), R1.2, R3.2 (WIPER)
unnamed: Q7.2 (E), R3.1 (CCW), R25.2
unnamed: Q7.1 (B), R4.2 (WIPER)
unnamed: Q9.1 (B), R13.2 (WIPER)
unnamed: Q6.1 (B), R5.1, R6.2, R7.1
unnamed: Q4.2 (E), R30.2
unnamed: J1.D3 (*D3), Q1.4 (G)
unnamed: Q8.2 (E), R10.2, R12.2 (WIPER)
unnamed: Q9.2 (E), R11.2, R12.1 (CCW)
unnamed: J1.SDA, R22.2, U1.4 (SDA), U2.4 (SDA), U3.4 (SDA)
unnamed: Q8.1 (B), R14.1, R15.2, R16.1
unnamed: Q9.3 (C), R21.1, Y+.TP
unnamed: Q8.3 (C), R18.1, Y-.TP
unnamed: R16.2, U3.1 (VOUT)
unnamed: J1.D2, U2.6 (AO)
unnamed: J1.D4, U3.6 (AO)
unnamed: J1.A0, R9.2, R31.1
unnamed: D6.A, Q1.5 (D), Q1.6 (D), Q1.7 (D), Q1.8 (D), U$1.P$4
unnamed: D4.A, U$1.P$2
unnamed: Q2.5 (D), Q2.6 (D), Q2.7 (D), Q2.8 (D), U$2.3 (IP-), U$2.4 (IP-)
unnamed: U$2.1 (IP+), U$2.2 (IP+), X5.2
unnamed: J1.D5 (*D5), Q2.4 (G)
unnamed: D1.A, JP1.1, Q3.5 (D), Q3.6 (D), Q3.7 (D), Q3.8 (D), U$3.P$3
unnamed: JP1.2, U$3.P$2
unnamed: D1.C, R2.1, U$3.P$1
unnamed: D3.A, U$3.P$6
unnamed: C2.2, D3.C, HV+.TP, R26.P$2 (2)
unnamed: R28.1, R33.2, U4.5 (SCK)
unnamed: D6.C, R19.1, U$1.P$1
unnamed: Q4.1 (B), R23.1, R24.2, R27.1
unnamed: R27.2, U1.1 (VOUT)
unnamed: J1.SCL, R32.2, U1.5 (SCL), U2.5 (SCL), U3.5 (SCL)
unnamed: FOCUS.TP, Q4.3 (C), R29.1
unnamed: R34.1, R35.2, U4.6 (!CS)
unnamed: J1.D9 (*D9), Q3.4 (G)
unnamed: J1.D10 (*D10), R28.2
unnamed: J1.A2, R20.2, R26.P$1 (1)
unnamed: Q5.5 (D), Q5.6 (D), Q5.7 (D), Q5.8 (D), X6.2
unnamed: J1.D11 (*D11), Q5.4 (G)
unnamed: J1.A3, U$2.7 (VOUT)
unnamed: J1.D12, R34.2
unnamed: J1.D7, U1.6 (AO)
unnamed: J1.D8, U4.7 ((MI)SO)
unnamed: U4.2 (T-), Y+1.TP
unnamed: U4.3 (T+), Y+2.TP
unnamed: J1.3.3V, U4.4 (VCC)
VCCINT: C1.1, D4.C, R8.2, R17.2, R18.2, R21.2, R29.2, R31.2

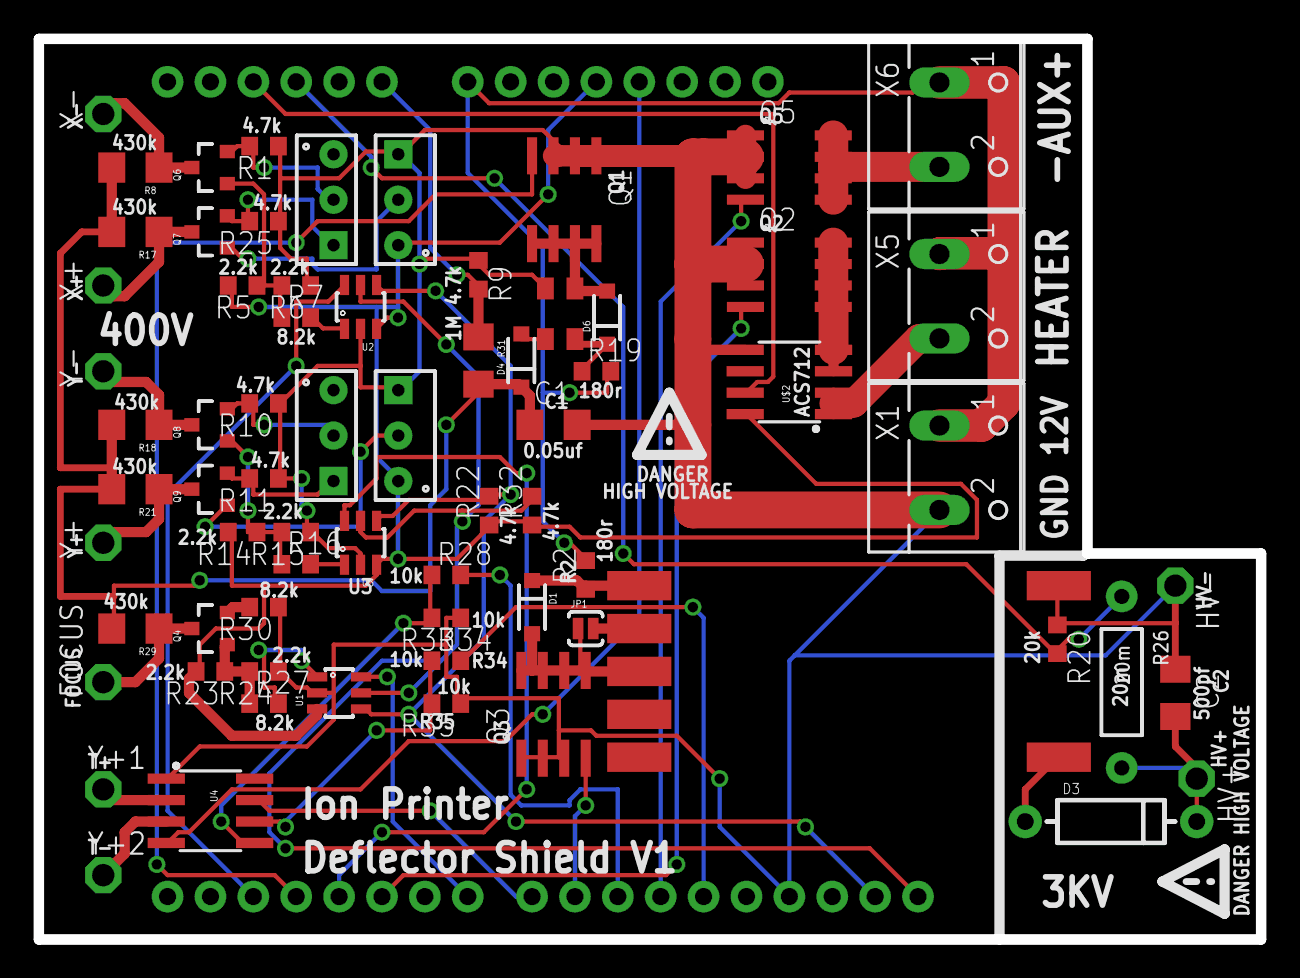
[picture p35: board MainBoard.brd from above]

Board: 2 copper layers, 72.4 x 53.3 mm, 71 parts (0 on the bottom side), 53 nets.

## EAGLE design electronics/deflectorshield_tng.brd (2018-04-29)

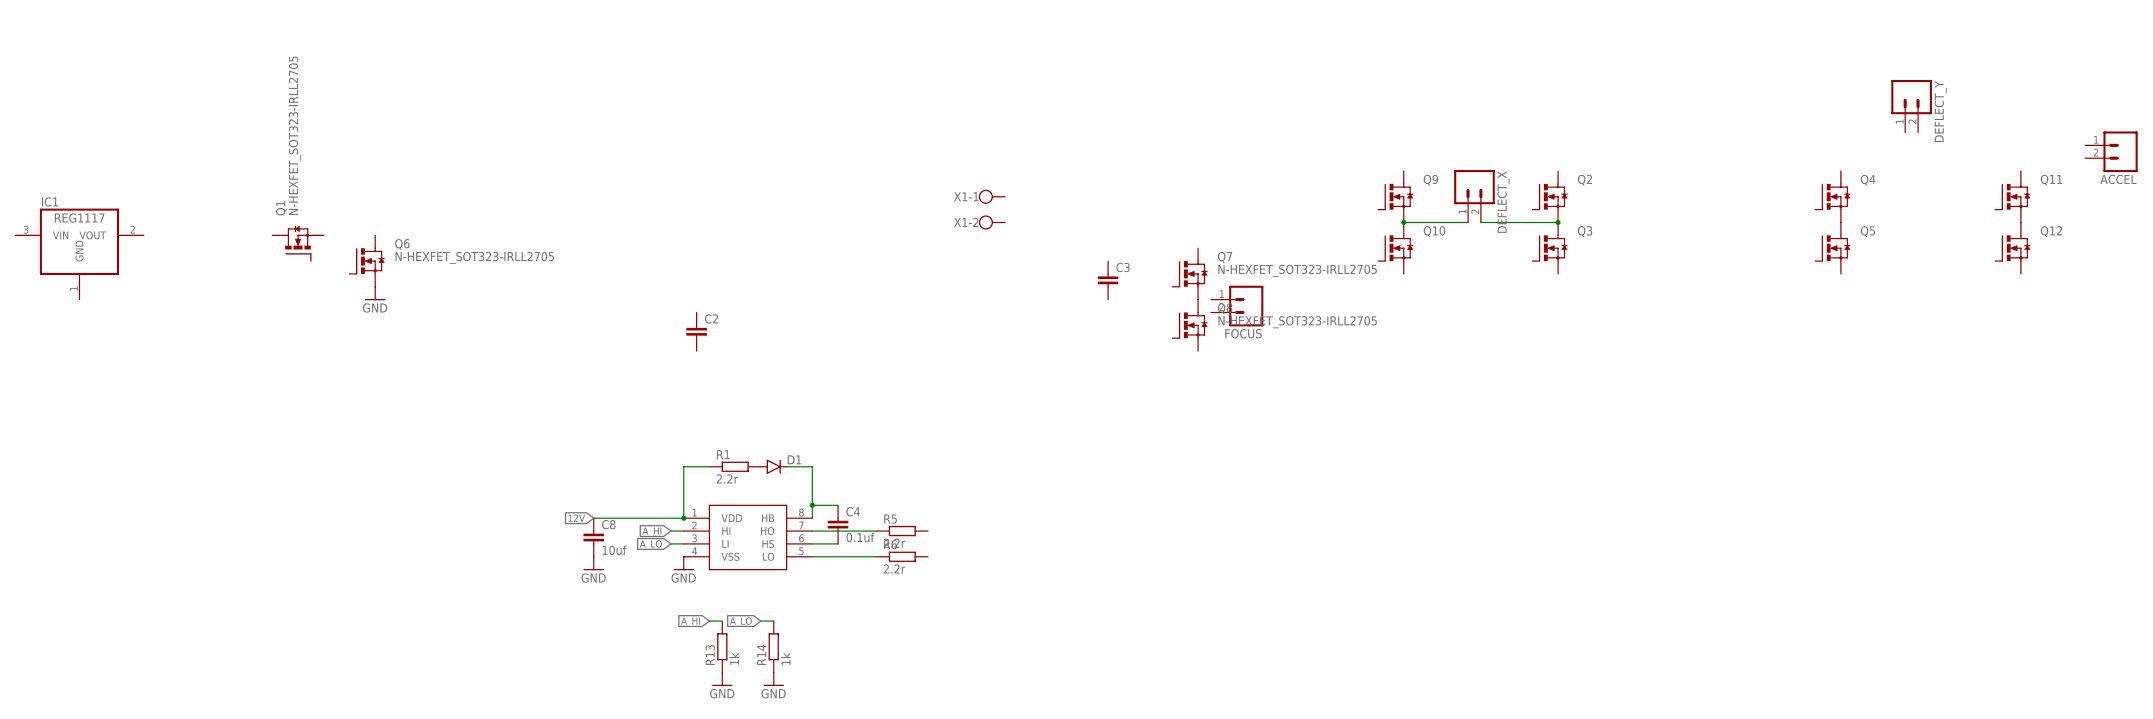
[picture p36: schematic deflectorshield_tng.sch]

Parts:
ACCEL: M023.5MM; SCREWTERMINAL-3.5MM-2
C2, C3: C-EUC0805; C0805
C4: 0.1uf; C0603
C8: 10uf; C0805
D1: DIODESMA; SMA-DIODE
DEFLECT_X: M023.5MM; SCREWTERMINAL-3.5MM-2
DEFLECT_Y: M023.5MM; SCREWTERMINAL-3.5MM-2
FOCUS: M023.5MM; SCREWTERMINAL-3.5MM-2
IC1: REG1117; SOT223
Q1, Q2, Q3, Q4, Q5, Q6, Q7, Q8, Q9, Q10, Q11, Q12: N-HEXFET_SOT323-IRLL2705; SOT223
R1, R5, R6: 2.2r; R1210
R13, R14: 1k; R0603
U$2: LM5109; SOIC8
X1: W237-102

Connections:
12V: C8.1, R1.1, U$2.1 (VDD)
A_HI: R13.2, U$2.2 (HI)
A_LO: R14.2, U$2.3 (LI)
GND: C8.2, IC1.1 (GND), Q6.3 (S), R13.1, R14.1, U$2.4 (VSS)
unnamed: DEFLECT_X.2, Q2.3 (S), Q3.4 (D)
unnamed: Q4.3 (S), Q5.4 (D)
unnamed: Q11.3 (S), Q12.4 (D)
unnamed: Q7.3 (S), Q8.4 (D)
unnamed: D1.A, R1.2
unnamed: C4.1, D1.C, U$2.8 (HB)
unnamed: C4.2, U$2.6 (HS)
unnamed: DEFLECT_X.1, Q9.3 (S), Q10.4 (D)
unnamed: R5.1, U$2.7 (HO)
unnamed: R6.1, U$2.5 (LO)

Board: 2 copper layers, 29 parts (0 on the bottom side), 14 nets, no tracks yet.

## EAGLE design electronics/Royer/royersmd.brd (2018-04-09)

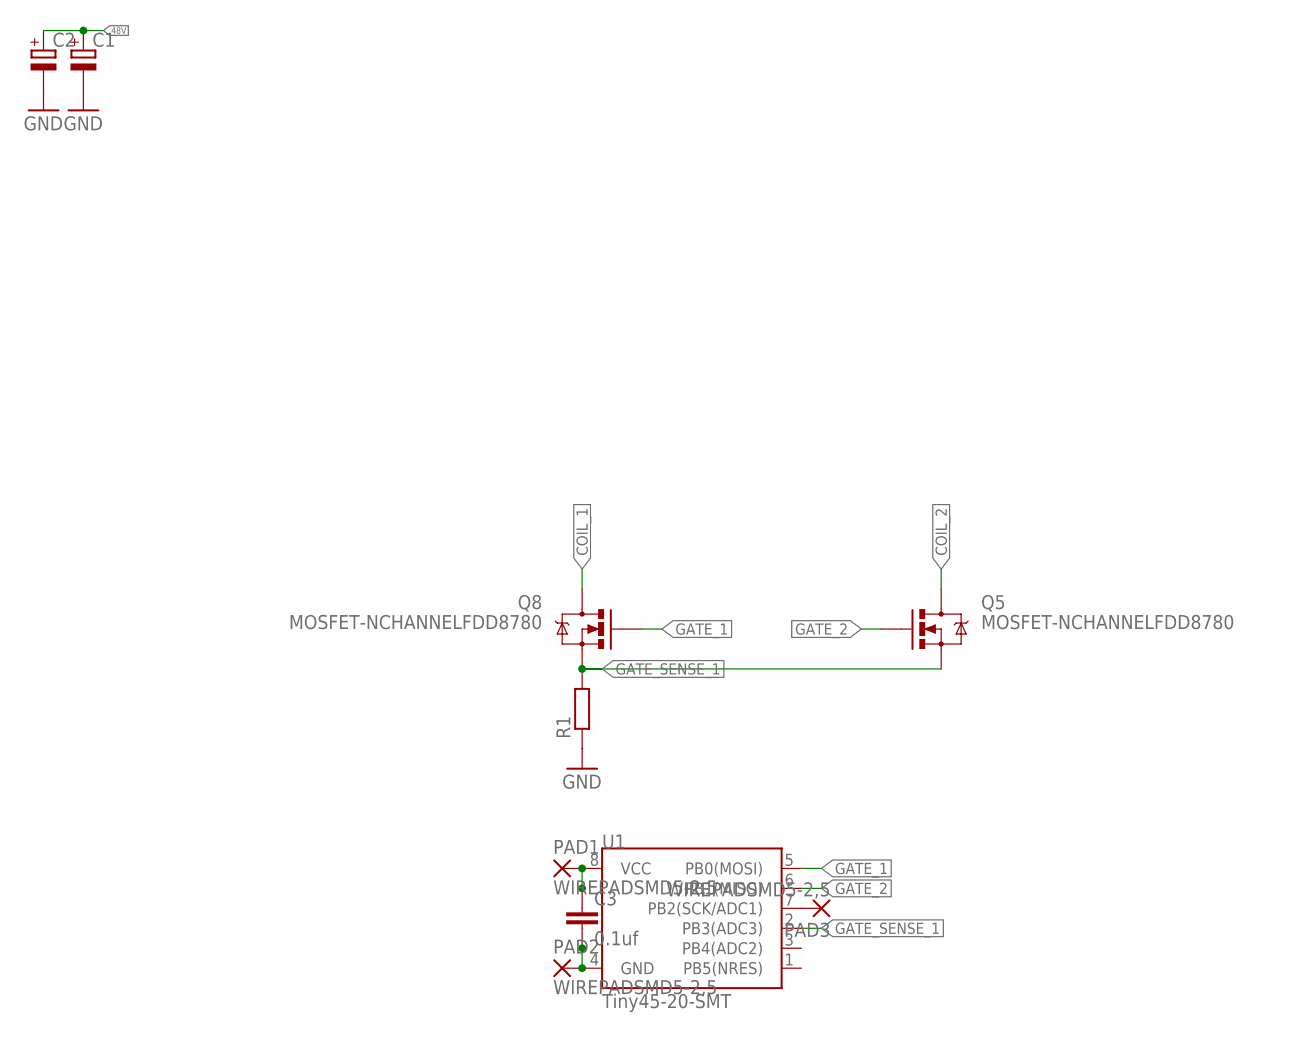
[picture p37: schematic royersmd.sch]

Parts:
C1, C2: CPOL-EUSANYO_9F; SANYO-OSCON_9F
C3: 0.1uf; C0603
PAD1, PAD2, PAD3: WIREPADSMD5-2,5; 5-2,5
Q5, Q8: MOSFET-NCHANNELFDD8780; DPAK
R1: R-EU_M1206; M1206
U1: Tiny45-20-SMT; SO08-EIAJ

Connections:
48V: C1.+, C2.+
COIL_1: Q8.4 (D)
COIL_2: Q5.4 (D)
GATE_1: Q8.1 (G), U1.5 (PB0(MOSI))
GATE_2: Q5.1 (G), U1.6 (PB1(MISO))
GATE_SENSE_1: Q5.3 (S), Q8.3 (S), R1.2, U1.2 (PB3(ADC3))
GND: C1.-, C2.-, R1.1
unnamed: PAD3.1, U1.7 (PB2(SCK/ADC1))
unnamed: C3.1, PAD1.1, U1.8 (VCC)
unnamed: C3.2, PAD2.1, U1.4 (GND)

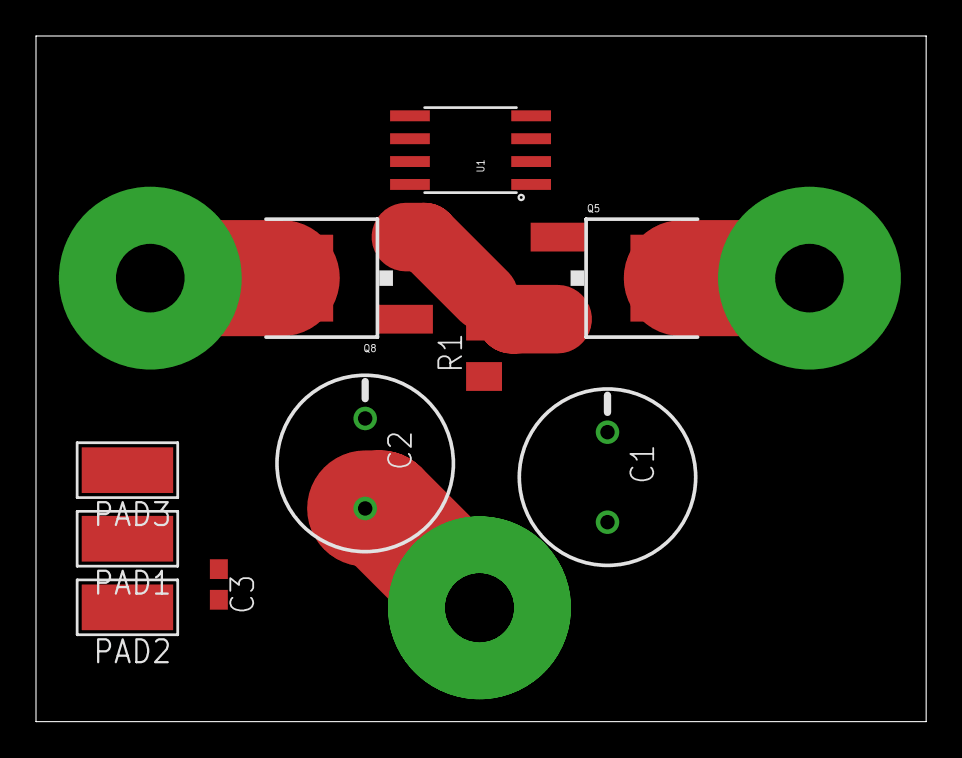
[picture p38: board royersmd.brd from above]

Board: 2 copper layers, 49.5 x 38.1 mm, 10 parts (0 on the bottom side), 8 nets.

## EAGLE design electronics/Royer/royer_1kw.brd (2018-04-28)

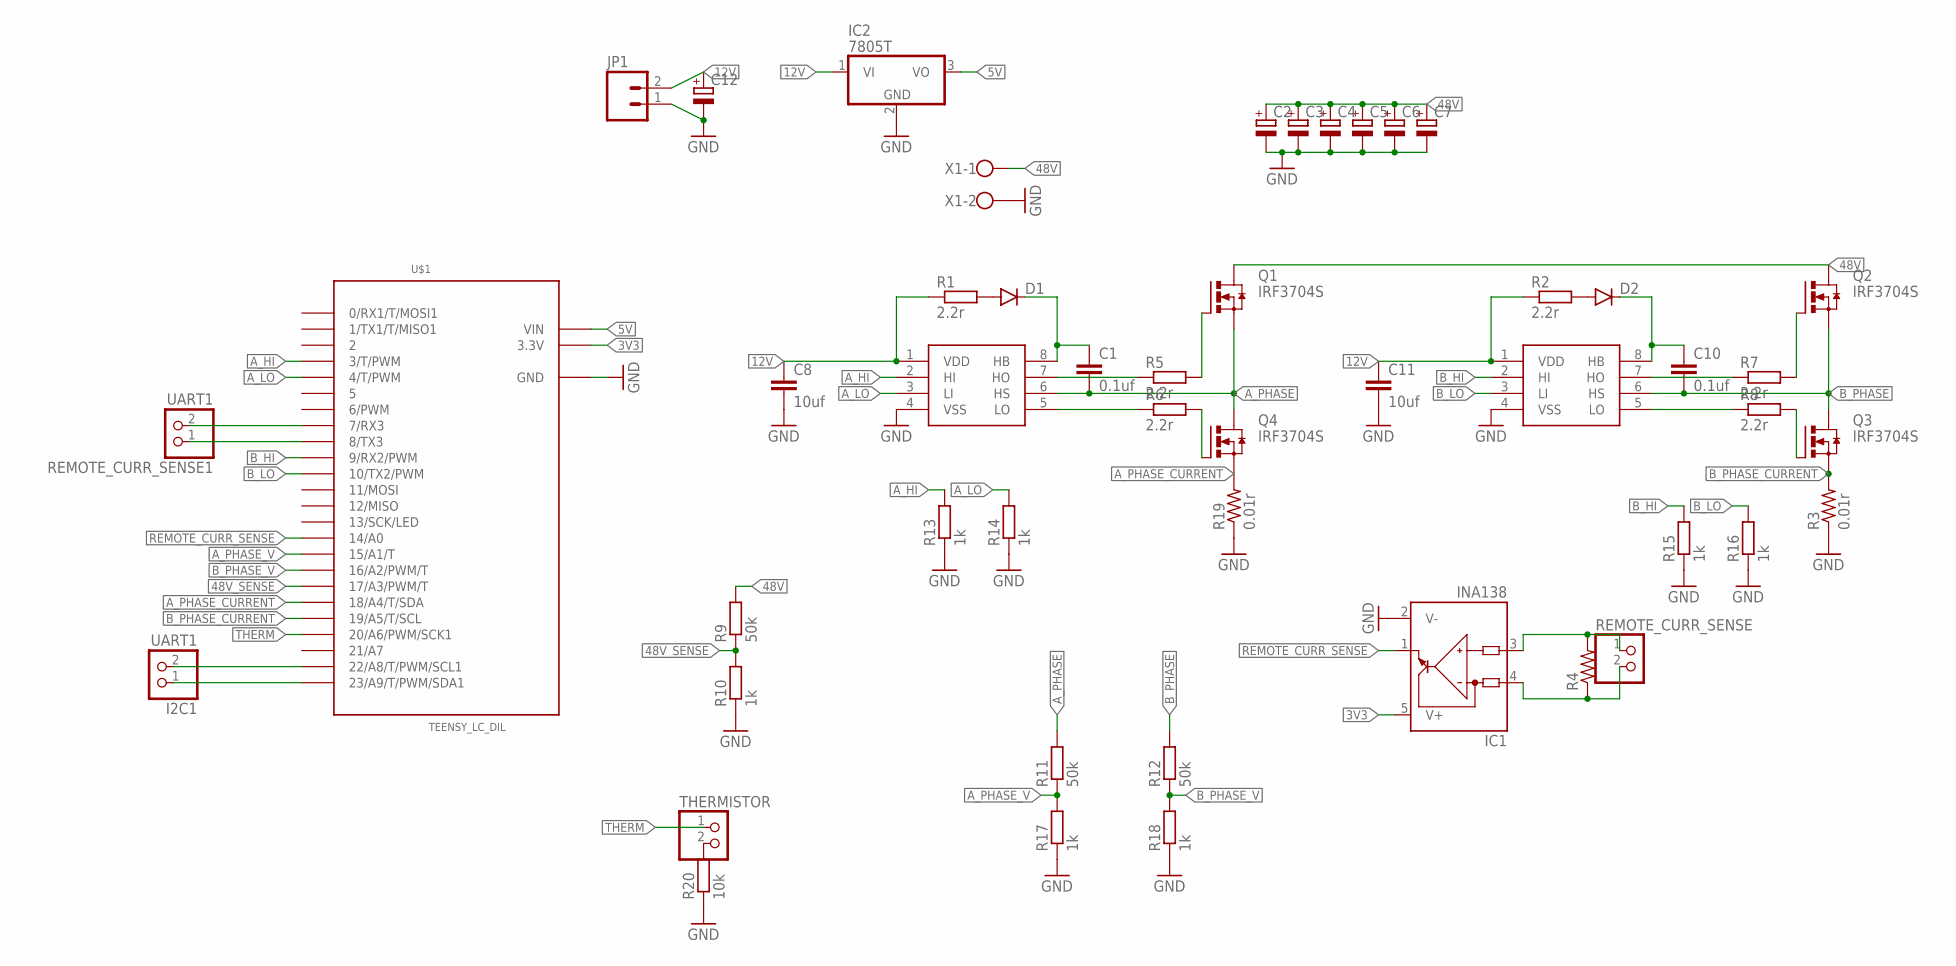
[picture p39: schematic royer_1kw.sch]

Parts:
C1, C10: 0.1uf; C0603
C2, C3, C4, C5, C6, C7: CPOL-EUE7.5-16; E7,5-16
C8, C11: 10uf; C0805
C12: CPOL-EUE2.5-7; E2,5-7
D1, D2: DIODESMA; SMA-DIODE
I2C1: UART1; 1X02
IC1: INA138; SOT23-5
IC2: 7805T; TO220H
JP1: M023.5MM; SCREWTERMINAL-3.5MM-2
Q1, Q2, Q3, Q4: IRF3704S; D2PACK
R1, R2, R5, R6, R7, R8: 2.2r; R1210
R3, R19: 0.01r; R3225
R4: RESISTOR1206; 1206
R9, R11, R12: 50k; R0603
R10, R13, R14, R15, R16, R17, R18: 1k; R0603
R20: 10k; R0603
REMOTE_CURR_SENSE: PINHD-1X2; 1X02
REMOTE_CURR_SENSE1: UART1; 1X02
THERMISTOR: PINHD-1X2; 1X02
U$1: TEENSY_LC_DIL; TEENSY_3.0-3.2&LC_DIL
U$2, U$4: LM5109; SOIC8
X1: W237-102

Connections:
3V3: IC1.5 (V+), U$1.3.3V
5V: IC2.3 (VO), U$1.VIN
12V: C8.1, C11.1, C12.+, IC2.1 (VI), JP1.2, R1.1, R2.1, U$2.1 (VDD), U$4.1 (VDD)
48V: C2.+, C3.+, C4.+, C5.+, C6.+, C7.+, Q1.2 (D), Q2.2 (D), R9.2, X1.1
48V_SENSE: R9.1, R10.2, U$1.17/A3 (17/A3/PWM/T)
A_HI: R13.2, U$1.3 (3/T/PWM), U$2.2 (HI)
A_LO: R14.2, U$1.4 (4/T/PWM), U$2.3 (LI)
A_PHASE: C1.2, Q1.3 (S), Q4.2 (D), R11.2, U$2.6 (HS)
A_PHASE_CURRENT: Q4.3 (S), R19.2, U$1.18/A4 (18/A4/T/SDA)
A_PHASE_V: R11.1, R17.2, U$1.15/A1 (15/A1/T)
B_HI: R15.2, U$1.9 (9/RX2/PWM), U$4.2 (HI)
B_LO: R16.2, U$1.10 (10/TX2/PWM), U$4.3 (LI)
B_PHASE: C10.2, Q2.3 (S), Q3.2 (D), R12.2, U$4.6 (HS)
B_PHASE_CURRENT: Q3.3 (S), R3.2, U$1.19/A5 (19/A5/T/SCL)
B_PHASE_V: R12.1, R18.2, U$1.16/A2 (16/A2/PWM/T)
GND: C2.-, C3.-, C4.-, C5.-, C6.-, C7.-, C8.2, C11.2, C12.-, IC1.2 (V-), IC2.2 (GND), JP1.1, R3.1, R10.1, R13.1, R14.1, R15.1, R16.1, R17.1, R18.1, R19.1, R20.1, U$1.AGND (GND), U$1.GND, U$2.4 (VSS), U$4.4 (VSS), X1.2
unnamed: R7.1, U$4.7 (HO)
unnamed: R8.1, U$4.5 (LO)
unnamed: Q1.1 (G), R5.2
unnamed: Q4.1 (G), R6.2
unnamed: D1.A, R1.2
unnamed: C1.1, D1.C, U$2.8 (HB)
unnamed: IC1.3 (IN+), R4.2, REMOTE_CURR_SENSE.1
unnamed: Q2.1 (G), R7.2
unnamed: Q3.1 (G), R8.2
unnamed: D2.A, R2.2
unnamed: C10.1, D2.C, U$4.8 (HB)
unnamed: IC1.4 (IN-), R4.1, REMOTE_CURR_SENSE.2
unnamed: R20.2, THERMISTOR.2
unnamed: R5.1, U$2.7 (HO)
unnamed: R6.1, U$2.5 (LO)
unnamed: REMOTE_CURR_SENSE1.1, U$1.8 (8/TX3)
unnamed: REMOTE_CURR_SENSE1.2, U$1.7 (7/RX3)
unnamed: I2C1.1, U$1.23/A9 (23/A9/T/PWM/SDA1)
unnamed: I2C1.2, U$1.22/A8 (22/A8/T/PWM/SCL1)
REMOTE_CURR_SENSE: IC1.1 (OUT), U$1.14/A0
THERM: THERMISTOR.1, U$1.20/A6 (20/A6/PWM/SCK1)

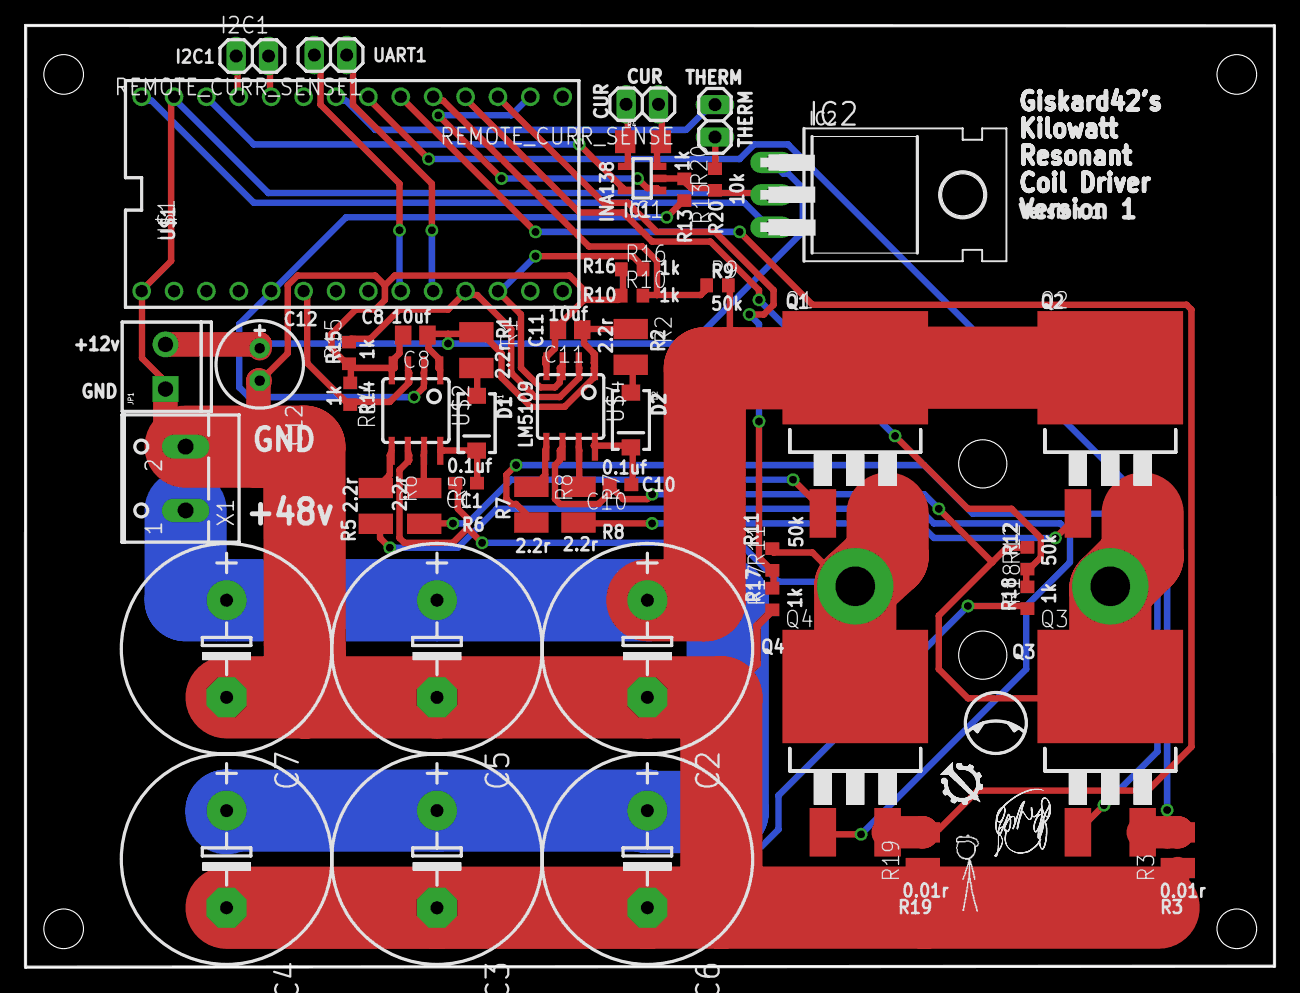
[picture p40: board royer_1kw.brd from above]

Board: 2 copper layers, 97.9 x 73.8 mm, 48 parts (0 on the bottom side), 37 nets.

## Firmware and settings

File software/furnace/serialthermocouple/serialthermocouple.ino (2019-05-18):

/*************************************************** 
  This is an example for the Adafruit Thermocouple Sensor w/MAX31855K

  Designed specifically to work with the Adafruit Thermocouple Sensor
  ----> https://www.adafruit.com/products/269

  These displays use SPI to communicate, 3 pins are required to  
  interface
  Adafruit invests time and resources providing this open source code, 
  please support Adafruit and open-source hardware by purchasing 
  products from Adafruit!

  Written by Limor Fried/Ladyada for Adafruit Industries.  
  BSD license, all text above must be included in any redistribution
 ****************************************************/

#include <SPI.h>
#include "Adafruit_MAX31855.h"

// Default connection is using software SPI, but comment and uncomment one of
// the two examples below to switch between software SPI and hardware SPI:

// Example creating a thermocouple instance with software SPI on any three
// digital IO pins.
#define MAXDO   3
#define MAXCS   4
#define MAXCLK  5

// initialize the Thermocouple
Adafruit_MAX31855 thermocouple(MAXCLK, MAXCS, MAXDO);

// Example creating a thermocouple instance with hardware SPI
// on a given CS pin.
//#define MAXCS   10
//Adafruit_MAX31855 thermocouple(MAXCS);
//small thermocouple
//#define P 1
//#define I 1
//#define D 4


#define P 0.75
#define I 0.5
#define D 6

double integral = 0;
double previous_error = 0;
float target = 0;

void setup() {
  while (!Serial); // wait for Serial on Leonardo/Zero, etc
  
  Serial.begin(115200);
  pinMode(13,OUTPUT);
  // wait for MAX chip to stabilize
  delay(500);
}

#define RAMP_1_TIME 300.0
#define RAMP_1_TEMP 350.0
#define HOLD_1_TIME (20.0*60.0)
#define RAMP_2_TIME (10.0*60.0)
#define RAMP_2_TEMP 1300.0
#define HOLD_2_TIME (60.0*60.0)

void loop() { 
   int current_time = millis()/1000UL;
   if(current_time < RAMP_1_TIME){ // ramp to 350 in 5 minutes
    target = (RAMP_1_TEMP*(current_time/RAMP_1_TIME));
   }
   else if((current_time-RAMP_1_TIME) < HOLD_1_TIME){
    target = RAMP_1_TEMP;
   }
   else if((current_time-RAMP_1_TIME-HOLD_1_TIME) < RAMP_2_TIME){
    target = (RAMP_2_TEMP*((current_time-(RAMP_1_TIME+HOLD_1_TIME))/RAMP_2_TIME));
   }
   else if((current_time-RAMP_1_TIME-HOLD_1_TIME-RAMP_2_TIME) < HOLD_2_TIME){
    target = RAMP_2_TEMP;
   }
   else{
    target = 0;
   }
   double current_temp = 0;
   for(int i=0;i < 5;i++){
      current_temp += thermocouple.readCelsius();
      delay(100); 
   }
   current_temp /= 5;
   if(current_temp != current_temp){
      return; //continue
   }
   double error = target-current_temp;
   integral += error*0.5; //100 ms
   double derivative = error-previous_error;
   integral = constrain(integral,-300,300);
   
   double output = P * error + integral*I + D*derivative;
   output = constrain(output,0,255);
   previous_error = error;
   analogWrite(13,output);
   Serial.println(String(current_time) + "," + String(target) + "," + String(current_temp) + "," + String(P*error) + "," + String(integral) 
                                  + "," +  String(derivative) + "," + String(output));
   
}

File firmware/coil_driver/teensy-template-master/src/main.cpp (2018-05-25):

#include "WProgram.h"

void zero_all(){
		digitalWrite(3,0);
		digitalWrite(4,0);
		digitalWrite(9,0);
		digitalWrite(10,0);
}

extern "C" int main(void)
{
	pinMode(3,OUTPUT);
	pinMode(4,OUTPUT);
	pinMode(9,OUTPUT);
	pinMode(10,OUTPUT);
//	analogWrite(3,127);
//	analogWrite(10,127);
	while (1) {
		zero_all();
		digitalWrite(3,1);
		digitalWrite(4,0);
		digitalWrite(9,0);
		digitalWrite(10,1);
		delay(1);
		zero_all();
		digitalWrite(3,0);
		digitalWrite(4,1);
		digitalWrite(9,1);
		digitalWrite(10,0);
		delay(1);

	}

}

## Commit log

2018-03-23 Reworked directory structure a bit
    [20mmTestCube_repaired.stl, 5mm_Calibration_Steps.stl, MainBoard.brd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]
2018-04-09 Better feedthrough design
    [chamber_RF_new_feeds.fcstd, chamber_ft2.fcstd, chamber_no_mounts_RF.fcstd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]
2018-04-20 New feedthroughs
    [RFInsulator1.stl, chamber_RF_new_feeds.fcstd, ftinsulator1.stl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]
2018-04-28 Royer seems to work.
    [chamber_RF_new_feeds.fcstd, rf_ftinsulator.fcstd, royer_1kw.brd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]
2018-04-29 Pruned a bit.
    [deflectorshield_tng.brd, deflectorshield_tng.sch]
2018-05-08 Going to simplify FTs a bit
    [rf_ftinsulator.fcstd]
2018-05-15 Fixing up insulator g code a bit
    [chamber_RF_new_feeds.fcstd, chamber_insulators_cutout.fcstd]
2018-05-17 Some reorganization
    [MainBoard.brd, MainBoard.sch, MainBoard_Simple.brd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]
2018-05-19 Something's broken with the ft backplate model.
    [FTInsulator1.fcstd, FTinsulator_backplate.fcstd, rf_ftinsulator.fcstd]
2018-05-25 Some more crucible details
    [FTinsulator_backplate.fcstd, rf_ftinsulator.fcstd]
2018-05-29 A different bowtie design
    [FTInsulator1.fcstd, FTinsulator_backplate.fcstd, RFInsulator1.stl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]
2018-06-02 More math.
    [bowtie_v2.step, chamber_RF_new_feeds.fcstd]
2018-06-05 Some more sources and simulations and I'm almost out of money fuck
    [chamber_RF_new_feeds.fcstd, chamber_RF_new_feeds_sim.fcstd, hc_ft_test.step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]
2018-06-06 Redesiging bowtie again
    [chamber_RF_new_feeds.fcstd]
2018-06-07 Working on automated mesh generation
    [bowtie_test_2.step, bowtie_test_2_bowtie.step, bowtie_test_2_fts.step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]
2018-06-07 Automated mesh generation and elmer heat visualization
    [bowtie_v3.step, bowtie_v3_simple.step, chamber_RF_new_feeds.fcstd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]
2018-06-07 Got bowtie mesh working...
    [bowtie_v3.step, chamber_RF_new_feeds.fcstd, just_fts.step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]
2018-06-17 More IBSIMU!
    [chamber_RF_new_feeds.fcstd, electrostatic.step]
2018-07-28 Yet another feedthrough revision
    [chamber_RF_new_feeds.fcstd]
2018-07-28 Cleaned up baseplate, added images
    [chamber_RF_new_feeds.fcstd]
2018-07-30 New wire fts done
    [chamber_RF_new_feeds.fcstd, new_wire_fts.fcstd]
2018-07-31 Some fixes to feedthrough toolpaths
    [new_wire_fts.fcstd, new_wire_fts_bottom.fcstd]
2018-10-11 Updated ibsimu tests
    [new_wire_fts.fcstd, new_wire_fts_bottom.fcstd]
2018-11-21 Hot cathode discussion
    [FTInsulator1_larger.fcstd, FTInsulator1_negative.fcstd, ceramic_wire_feedthroughs.fcstd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]
2018-11-24 Working ElmerFEM nozzle simulation
    [bowtie.step, bowtie.stl]
2018-11-25 Functional bowtie joule heating sim
    [bowtie.step]
2018-11-26 Still working on nozzle sim
    [FTInsulator1_negative_tall.fcstd, bowtie.step, ceramic_wire_feedthroughs_insert.fcstd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]
2018-11-26 Graphite values are in.
    [bowtie_2.fcstd, chamber_RF_new_feeds.fcstd]
2018-12-10 Working on new bowtie design
    [M353-502.stp, bowtie_2.fcstd, bowtie_3.fcstd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]
2018-12-13 New bowtie working admirably!
    [bowtie_3.fcstd, bowtie_3.step]
2018-12-13 Enthalpy heat flow accounted for...
    [bowtie_3.fcstd]
2018-12-14 looong boi
    [bowtie_3.fcstd, bowtie_3.step]
2018-12-14 This is not an improvement.
    [bowtie_3.fcstd, bowtie_3.step, bowtie_4.fcstd]
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2018-12-21 Magnetic field export from FEMM
    [aluminium_ft_insert.fcstd]
2018-12-28 A few more magnetic tests
    [aluminium_ft_insert.fcstd, chamber_RF_new_feeds.fcstd]
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2019-01-12 Bunch 'o nonsense part deux
    [chamber_RF_new_feeds.fcstd]
2019-01-13 Haha! BowtieML!
    [bowtie_3.fcstd, bowtie_5.fcstd]
2019-01-21 Tidied up the repo a bit
    [bowtie_5.fcstd]
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2019-02-10 Some more work on the beam sim
    [chamber_RF_new_feeds.fcstd]
2019-02-13 Working on WARP
    [chamber_RF_new_feeds.fcstd]
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2019-02-17 Some mesh gen automation
    [nozzle-ascii.stl, nozzle.stl, nozzle_test.fcstd]
2019-02-18 sparta's working - IT'S BEAUTIFUL
    [chamber_RF_new_feeds.fcstd, nozzle-ascii.stl, nozzle.stl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]
2019-02-18 Fixed gitignore?
    [nozzle.stl]
2019-02-21 Gauge code!
    [chamber_RF_new_feeds.fcstd, nozzle.stl, nozzle_test.fcstd]
2019-02-24 Reorganized everything a bit
    [nozzle_test.fcstd]
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2019-03-01 10k chamber modelling
    [gauge.csv]
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2019-03-03 More jupyter fixes!
    [mk_3_5.fcstd]
2019-03-05 Genetic algorithm stuff, more chamber plate stuff
    [mk_3_5.fcstd]
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2019-03-08 Made a small mistake with the baseplate
    [mk_3_5.fcstd]
2019-03-08 Fixed baseplate, working on current.
    [mk_3_5.fcstd]
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2019-03-09 More on scanning domain
    [mk_3_5.fcstd]
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2019-03-19 domain scanning working, though not in parallel.
    [gauge.csv]
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2019-04-02 Second pulldown, attempts at hot cathode production, etc
    [ceramic_standoff_test_1_cone.fcstd, coupler.scad, coupler_spider.scad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]
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2019-04-06 dxf import working, but this will take way too long.
    [solid.dxf]
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2019-04-19 Somewhat functional space charge compensation?
    [CER-4.stp, bowtie_prototype_1.FCStd, bowtie_prototype_1.step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]
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2019-04-19 Nope. Energy was sampled at wrong x position.
    [bowtie_prototype_1_milling.FCStd]
2019-04-21 Whew, that's fast! Using solution from uhoh.
    [bowtie_prototype_1.FCStd]
2019-04-25 Bowtie sim working again
    [bowtie_prototype_1.FCStd, bowtie_prototype_1_cut.step, solid.dxf]
2019-04-26 C++ poisson solver working
    [assembly.FCStd, solid.dxf]
2019-04-27 E-beam working based on paper!
    [solid.dxf]
2019-04-27 Heavy beam also mostly functional
    [solid.dxf]
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2019-05-01 More theory, beam diagnostics
    [bowtie_prototype_1_cut.step, bowtie_prototype_1_looong.FCStd, bowtie_prototype_1_reflector.step]
2019-05-05 Updated graphite resistivity value
    [assembly.FCStd, furnace_endplate.FCStd]
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2019-05-08 More work on multiphysics
    [bowtie_prototype_1_looong.FCStd, furnace_endplate.FCStd]
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2019-05-14 Unit testing and new kiln
    [assembly.FCStd, blocks.FCStd, bowtie_prototype_1_looong.FCStd]
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2019-05-29 directory structure's a little convoluted, wish I didn't need cmake
    [main.cpp]
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2019-08-14 If you're having kernel problems I feel bad for you son
    I got 99 p. but a kernel aint one
    [main.cpp]
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2019-10-27 Still working on data structure
    [cyl-MLI.scad, wall-MLI.scad]
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2020-02-19 Fixed a few things on the device data structure side
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2021-06-14 Resume, split out nyion
    [10mm_cube.obj]

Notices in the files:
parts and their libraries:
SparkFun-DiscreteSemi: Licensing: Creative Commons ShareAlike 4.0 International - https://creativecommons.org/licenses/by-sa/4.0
